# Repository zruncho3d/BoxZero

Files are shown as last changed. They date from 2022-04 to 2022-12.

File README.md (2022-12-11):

# BoxZero - a fully-boxed V0/T0/X0 mod

Simplify, strengthen, and seal your [Voron Zero](https://github.com/VoronDesign/Voron-0) or V0-derived printer ([Tri-Zero](https://github.com/zruncho3d/tri-zero), [Double Dragon](https://github.com/zruncho3d/double-dragon)) by ditching the tophat and moving to a full-box frame.

Mod an existing printer for ~$60 or build a BoxZero from scratch, keeping the 200mm extrusions of a stock V0 frame kit, at about the same cost.

Retains the same footprint as a stock V0, but comes in a bit taller, with more space for the umbilical.

Pairs exquisitely with [Tri-Zero](https://github.com/zruncho3d/tri-zero) (a triple-belted Z mod) and [ZeroPanels](https://github.com/zruncho3d/ZeroPanels) (clip-in, clip-out enclosure panels), both shown in the render and pics below, as well as [Double Dragon](https://github.com/zruncho3d/double-dragon) (the V0 IDEX mod).

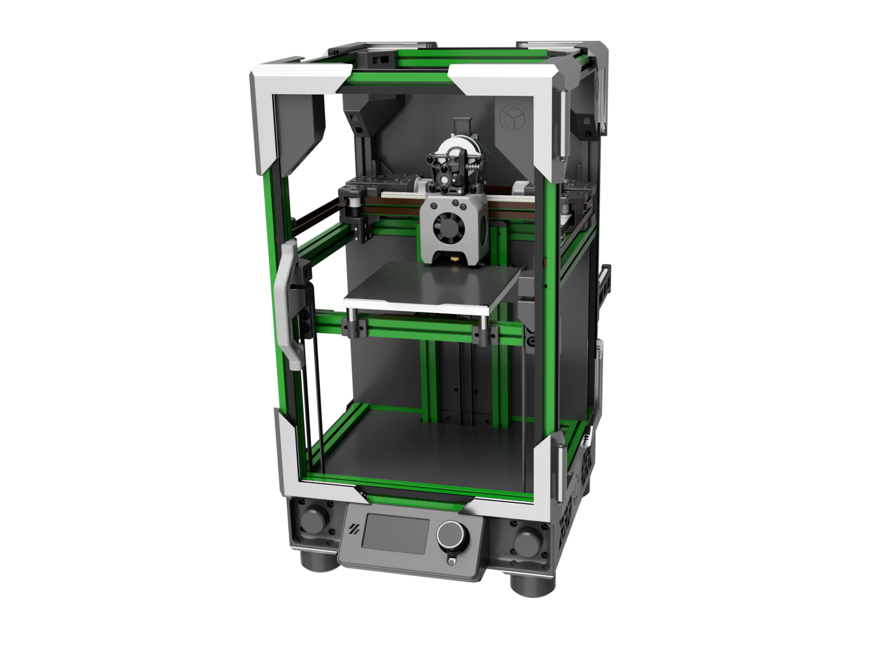
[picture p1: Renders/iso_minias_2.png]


It's real, tested, and reproduced independently the instructions in this repo.  Gallery:

| Zruncho's Green T0 Conversion | Iso View | Red5's Blue T0 Conversion | Iso View |
| - | - | - | - |
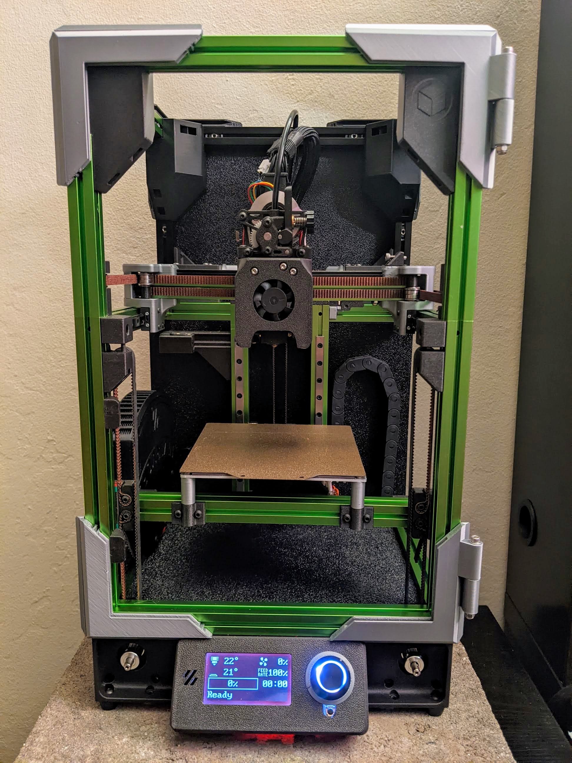
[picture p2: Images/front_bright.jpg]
Front
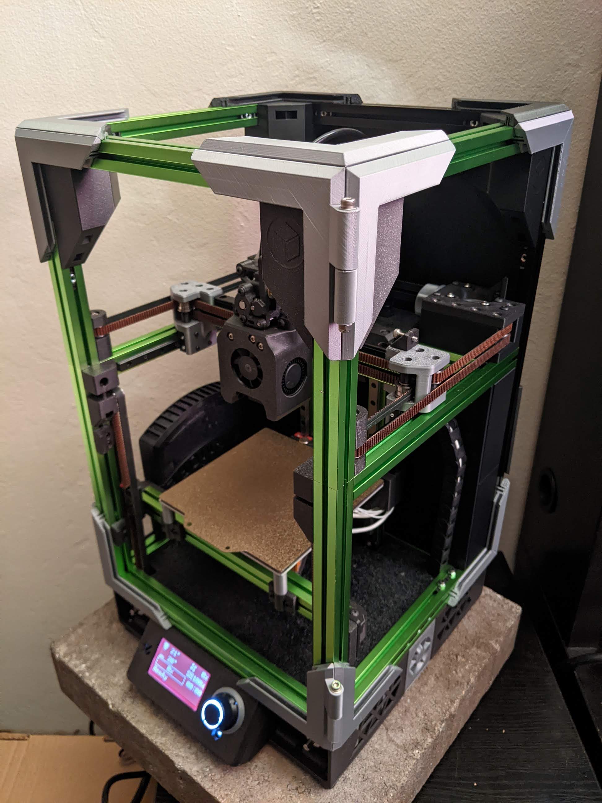
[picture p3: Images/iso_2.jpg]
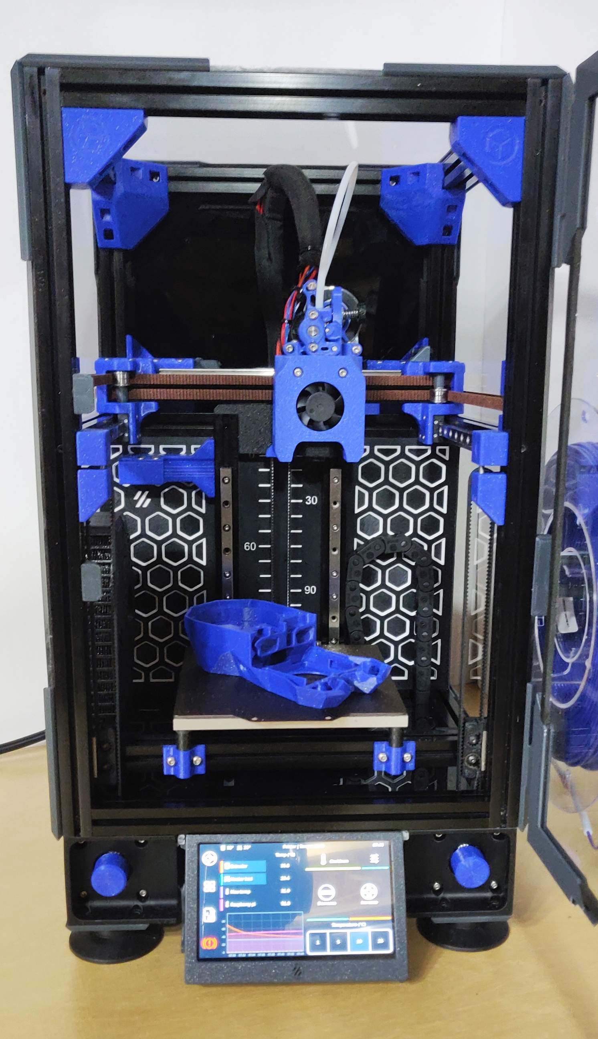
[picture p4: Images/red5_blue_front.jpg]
Front
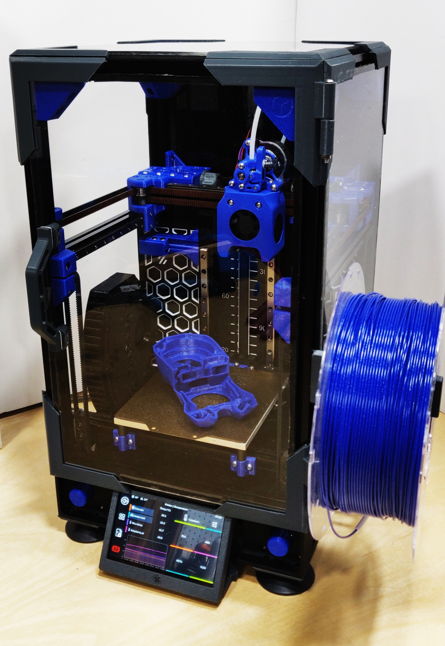
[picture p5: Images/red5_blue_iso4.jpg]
|  |  |  | |

Three key parts make this mod possible:

| AB Blocks (V0-derived) | Front Idlers (Double Dragon-derived) | Top Corners (new, optional) |
| - | - | - |
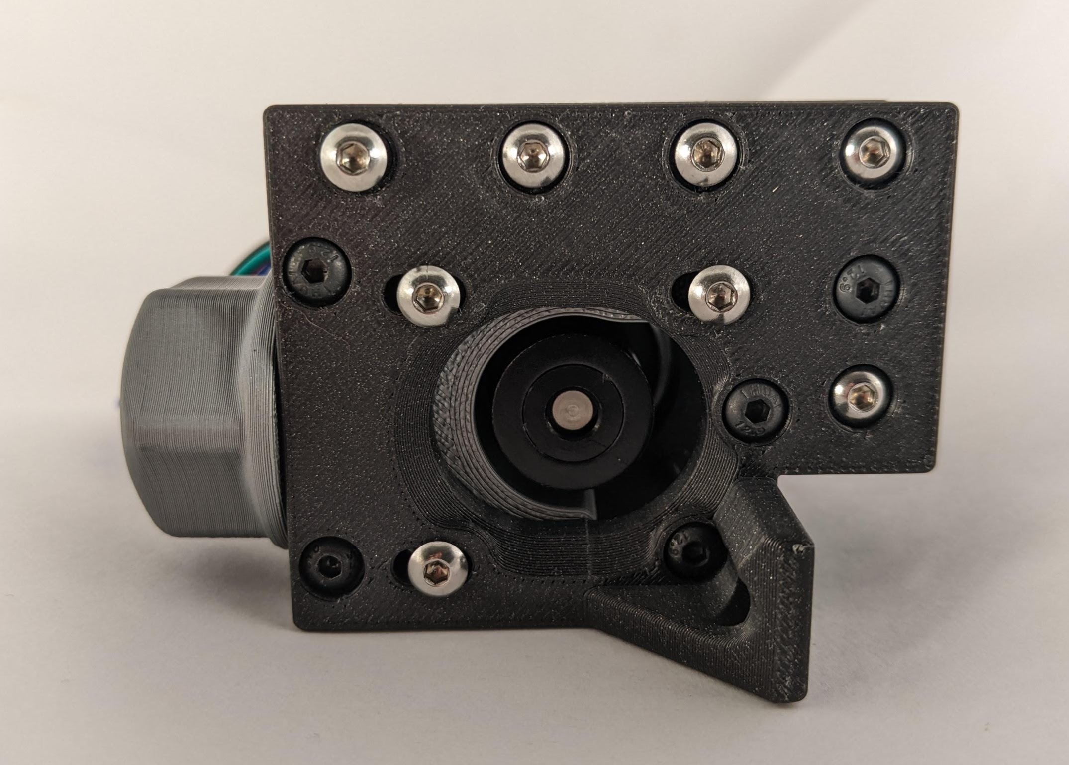
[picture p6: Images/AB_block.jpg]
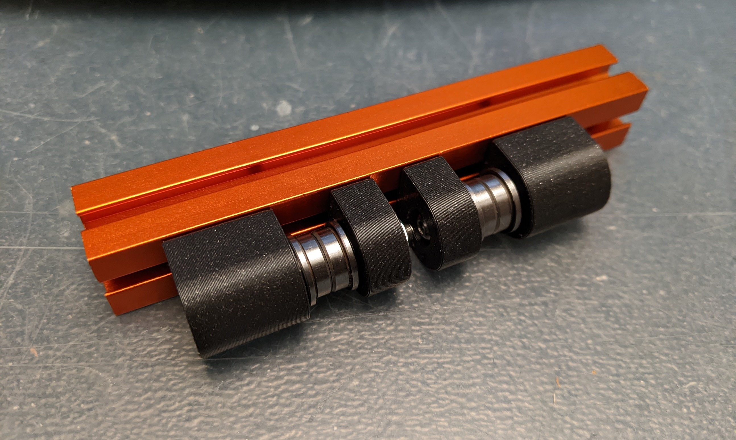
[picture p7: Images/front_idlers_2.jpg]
Front
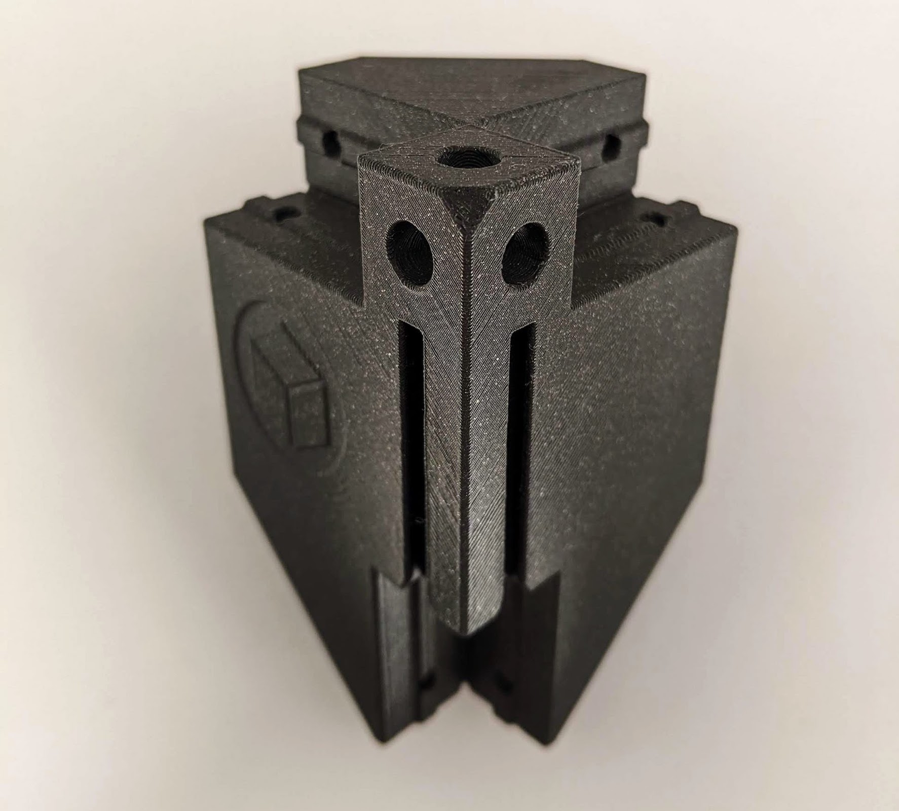
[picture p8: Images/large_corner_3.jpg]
|  |  |  |

Questions?

Join us on the `#tri-zero` channel on the [DoomCube Discord](https://discord.gg/doomcube) - to ask questions, or share your experiences with this mod!

## Updates

#### 2022-04-18 First Release, Alpha-1!

Hello World, BoxZero.

See how it compares, visually:

| BoxZero +TriZero +ZeroPanels +MiniAS +12864 | BoxZero +ZeroPanels | Voron Zero with Tophat (stock V0.1) |
| - | - | - |
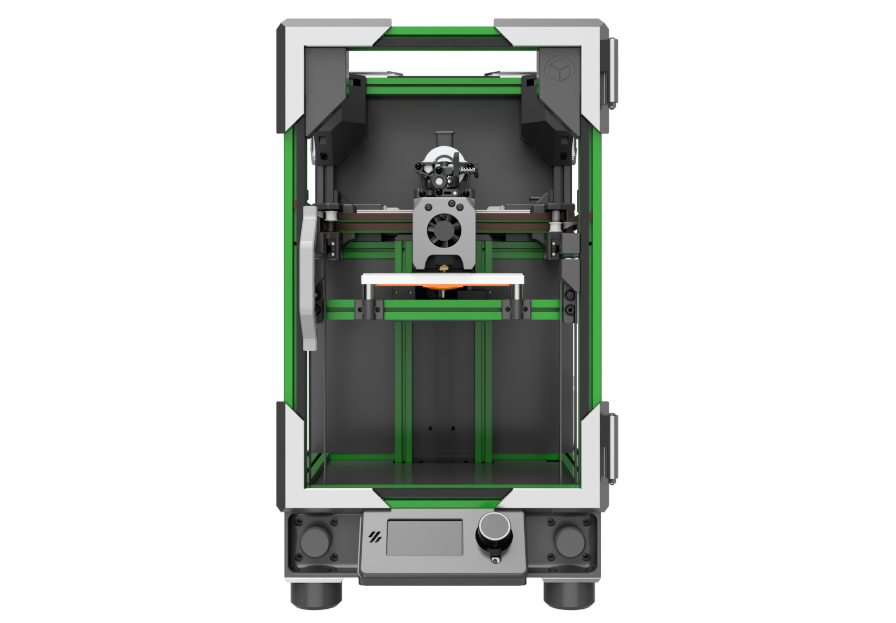
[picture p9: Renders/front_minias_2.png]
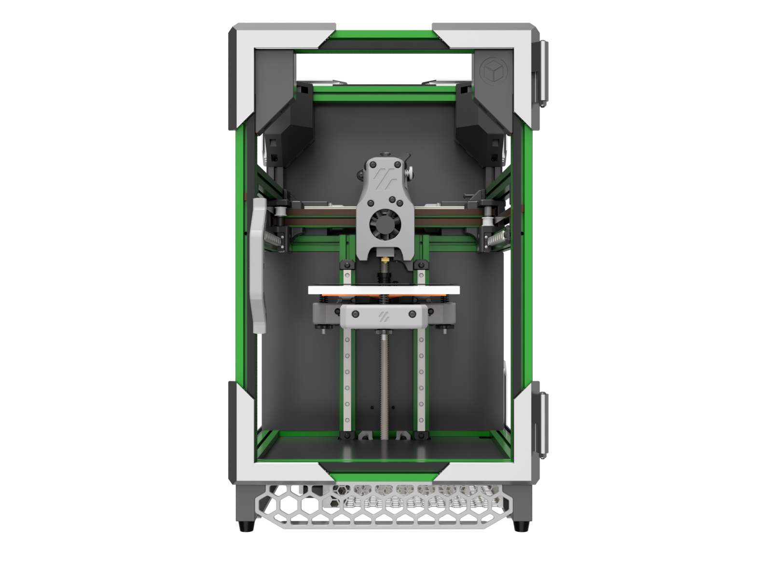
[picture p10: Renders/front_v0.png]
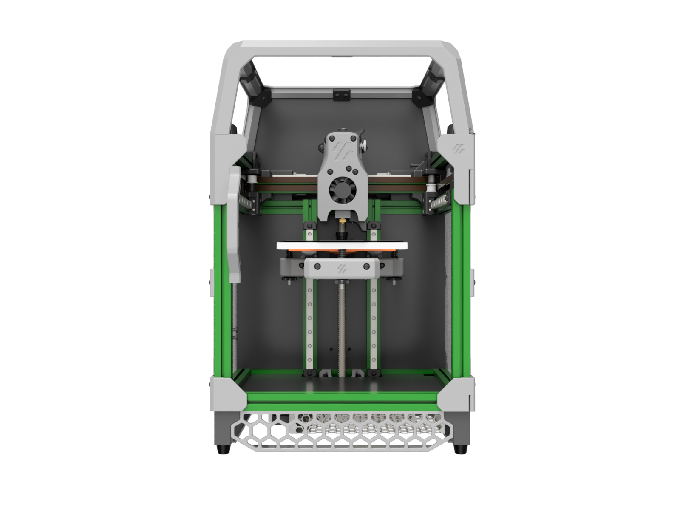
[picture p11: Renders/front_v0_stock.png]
|   |  | 
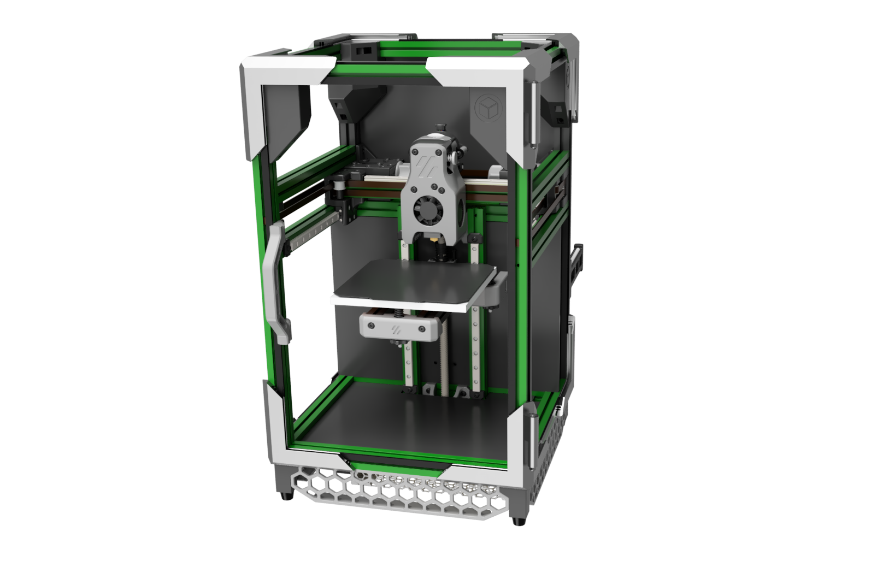
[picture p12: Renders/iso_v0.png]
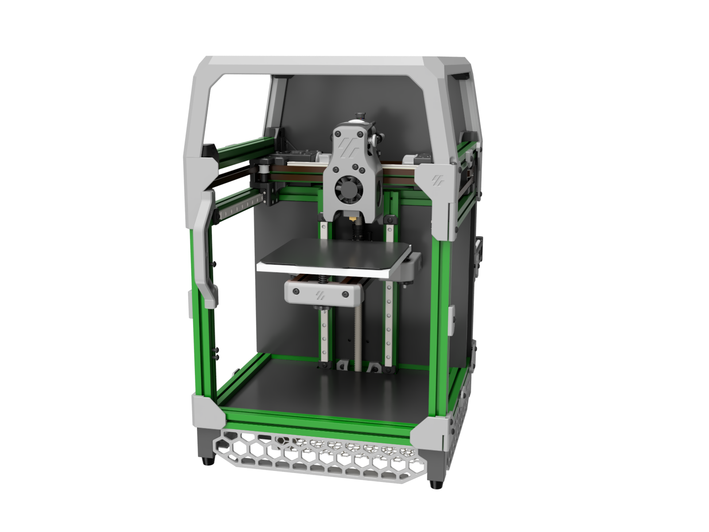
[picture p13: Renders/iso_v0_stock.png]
| Iso  |  | 

## Why this mod?

The V0 tophat serves its function: to enclose the printer.

But ask a bunch of V0 owners... and let's just say, few will express their undying love for the tophat.  

Some actual unsolicited quotes, heard in just the last week:
>  "Yeah, the tophat is kind of the bane of my V0 experience"

> "Can you tell I really dislike the tophat? They started bugging me less after I added a hinged riser that is a solid square. It does not match well enough so it looks bad that way but the stiffness and hinges are what the original should have had."

While I think it looks fine, the V0 tophat creates real quality-of-life issues in practice:
* It's a notoriously challenging print that requires the entire bed of a Voron Zero and good bed adhesion and leveling.
* The small trapezoidal panels are harder to source than rectangular parts.
* The design adds many small parts to print and many heatsets to add.
* To clear the umbilical with some toolhead mods (e.g. [Mini-AfterSherpa](https://github.com/KurioHonoo/Mini-AfterSherpa)), a tophat extension is needed, ideally a [hinged one](https://github.com/zruncho3d/VoronUsers/tree/hinged_tophat/printer_mods/zruncho/Hinged_Tophat_Riser).  But those "censor the view" and require even more parts to print and source.
* It doesn't scale easily.  You can add extensions ([X0 example](https://github.com/zruncho3d/double-dragon/blob/main/STLs/Optional/Tophat_Middle_Spacer_x2.stl)), but you really want to increase the beam thickness too, and not need extensions to fit a V0 plate.
* You can't mount stuff to it easily, at least compared to extrusions (like lights or a camera).

## How does this mod work?

This mod ditches the tophat, moves to a fully-boxed frame, and then updates each part affected by the change to fit best in the remaining space.

### Frame and Corners

You will need additional extrusions to box the frame and make a "fixed tophat".  Don't worry though, you can easily add a hinged top panel, or even just pop out toolless-ly when desired.

Here is the extra extrusion content, visualized:

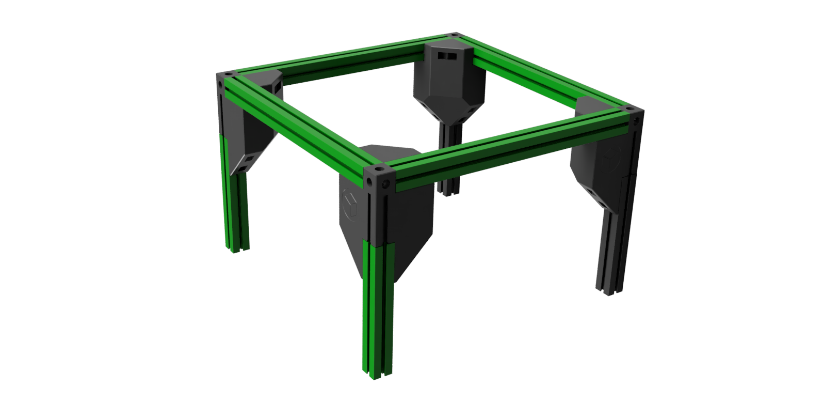
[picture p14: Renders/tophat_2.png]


You can keep your colored extrusions from a V0 frame kit by joining 100mm ones from the bed to 200mm ones in the front.  This repo even includes a printed "extrusion wrench" to join extrusions without marring the surface.

Or, you can use off-the-shelf 300mm-long 1515 extrusions and add the blind joint holes yourself, easily.  With printed corners that add 50mm of height, you'll then have enough clearance for the umbilical.

Or, you can use a full-blind-joints frame with taller extrusions (350mm or taller) and optionally strengthen the corners with corner stiffeners.  These stiffeners are recommended for larger sizes than V0-stock, especially 250mm-length-extrusion printers.

| Large Corner (adds 50mm height) | Small Corner Stiffener |
| - | - |
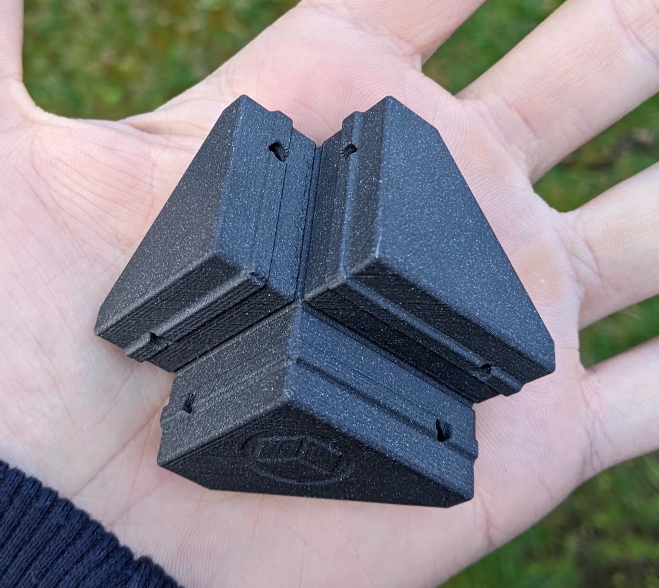
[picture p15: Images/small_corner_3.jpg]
| Front |  |

The V0 side extrusions and bed extrusions get lifted, then other extrusions take their place.  There are a few options:

* **Option A: Replace all verticals with 300s**.  Move 2 of the existing 200s to the top.
* **Option B: Replace the rear 2 verticals with 300s**.  Move 2 of the existing 200s to the top, then add 100mm extrusions to replace the ones for the bed and colorize the front.  
  * If you have a Kirigami bed or T0 mod, the 100s will be easily available.  
  * Conjoin the front 100 and 200mm extrusions with set screws an add 2 200mm extrusions on the side to span the gaps.
  * You'll still need an additional 200mm extrusion for the back.
* **Option C Mix of new 100 and 200mm-length extrusions**.  Effectively, add a fixed tophat like the render above.
* **Option D: Go full-height with cut-to-size extrusions**.  Then use the smaller stiffeners, vs the full-size extrensions.

It all depends on what's easiest to source and what you think looks best.  You choose.  Either way, it should feel super-rigid after.

Note that the corners are asymmetric, with a logo on only one side... we don't want an [M1 situation](https://en.wikipedia.org/wiki/BMW_M1) here.

### AB Blocks

The packaging of the V0 is super-tight, so the big challenge with a full box is fitting the belt path around added frame extrusions.  The key insight was to add extra F623 bearings to redirect the belts around the rear extrusion verticals.  To free up space for the belt, the sliding motor block had to be chopped, but the 3 remaining screws are plenty to fully secure the motor.

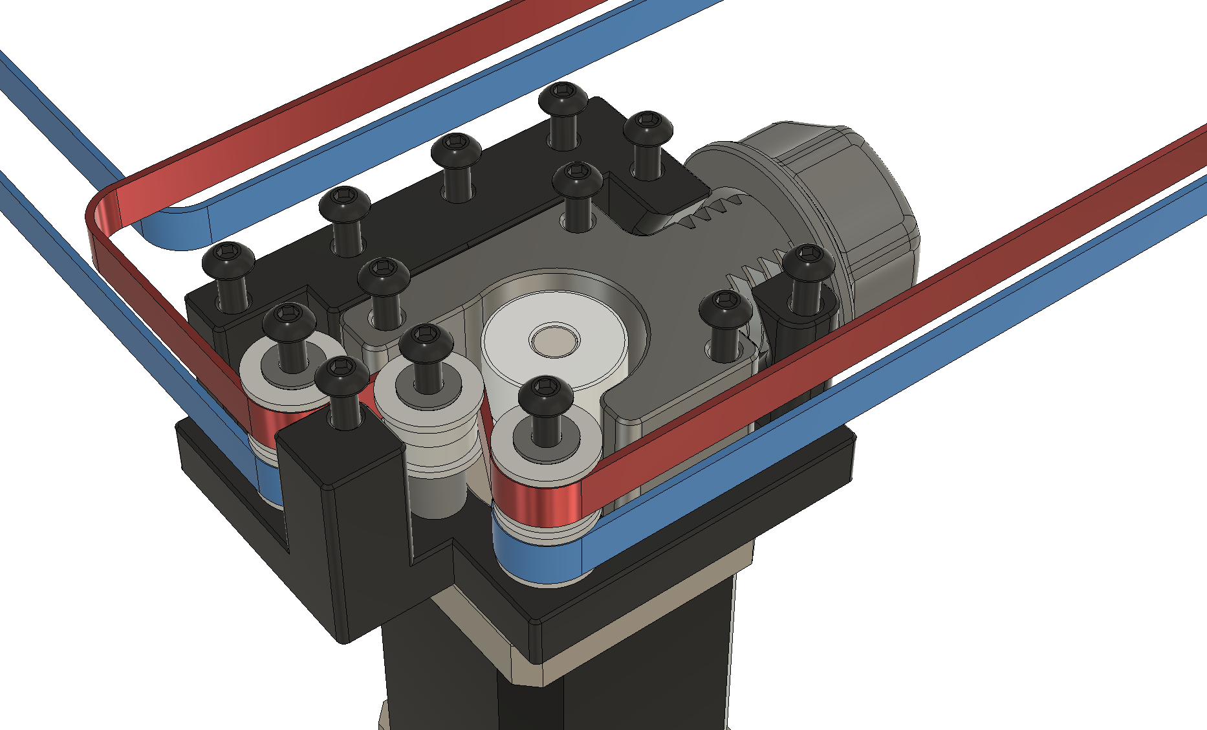
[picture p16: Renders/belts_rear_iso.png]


Top view:

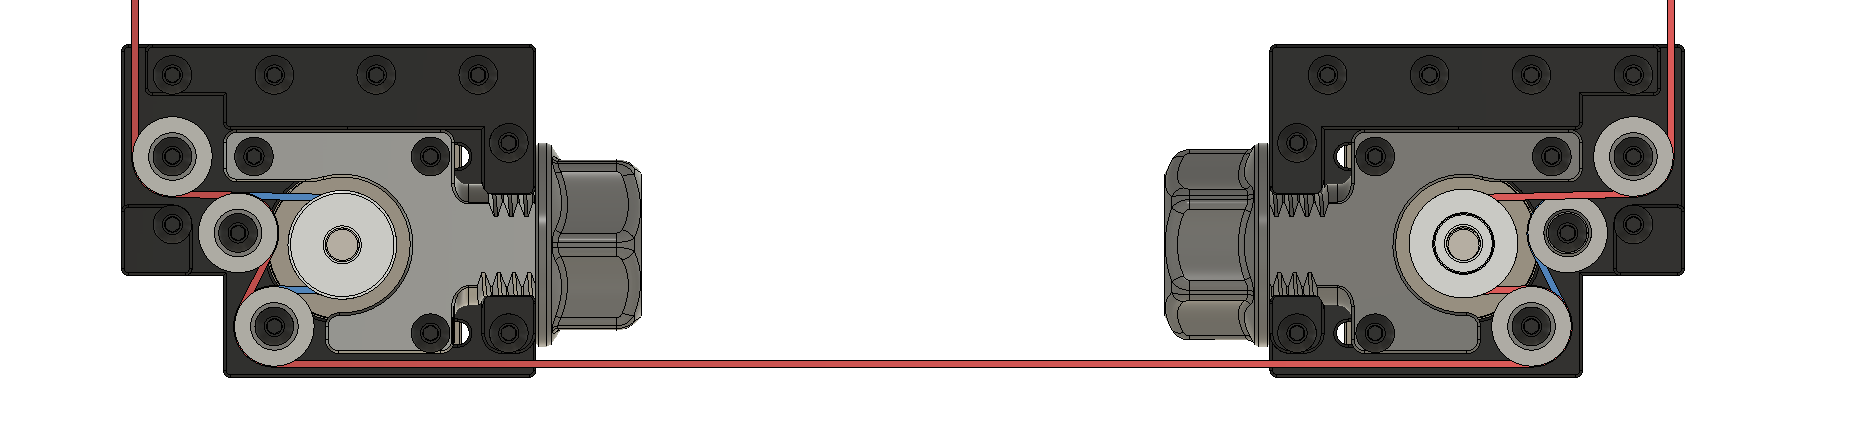
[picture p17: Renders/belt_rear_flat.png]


The complete AB blocks:

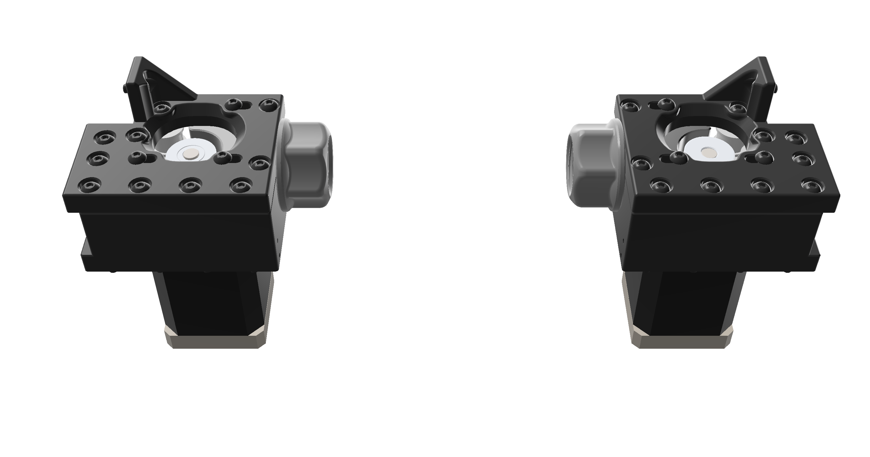
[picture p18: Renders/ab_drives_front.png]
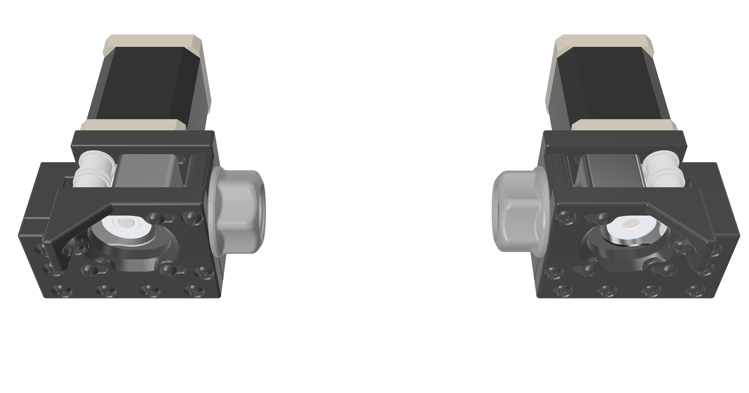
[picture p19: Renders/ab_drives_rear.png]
|  |  |
| - | - |

The new AB blocks are intentionally set back 3mm from the front, to support future mods to add extra Y travel from an offset gantry, so you'll want to add something to bridge that 3mm gap to the Y endstop.  [F0 MGN9 spacers](https://github.com/zruncho3d/f-zero/blob/main/STLs/Gantry/mgn9_spacer_x2.stl) are one easy to span it, especially if using a non-levered microswitch.

The hole positions have been moved too, so that all are aligned easily with 15mm No-Drop nuts.

### Front Idlers

At the front, this mod uses slightly modified [Double Dragon](https://github.com/zruncho3d/double-dragon) front Y idlers for the main belts.

Front

### Enclosure

You can use the default V0 enclosure parts, or much better, can move to [ZeroPanels](https://github.com/zruncho3d/ZeroPanels), which clip in without screws, nuts, magnets, or tape. They're perfect for this application.

[Tecnologic's full boxed-frame enclosure](https://github.com/Tecnologic/ZeroPanels/tree/main/Mods/tecnologic/FlyingZero300), based on the original ZeroPanels, works perfectly here and even includes high-strength, 270-degree hinges.  What's not to love?  You can put the hinges on top too... BAM, and you have a fully accessible toolhead, without even needing 5 seconds to clip out a panel.

| Main Corners | Hinge Corners |
| - | - |
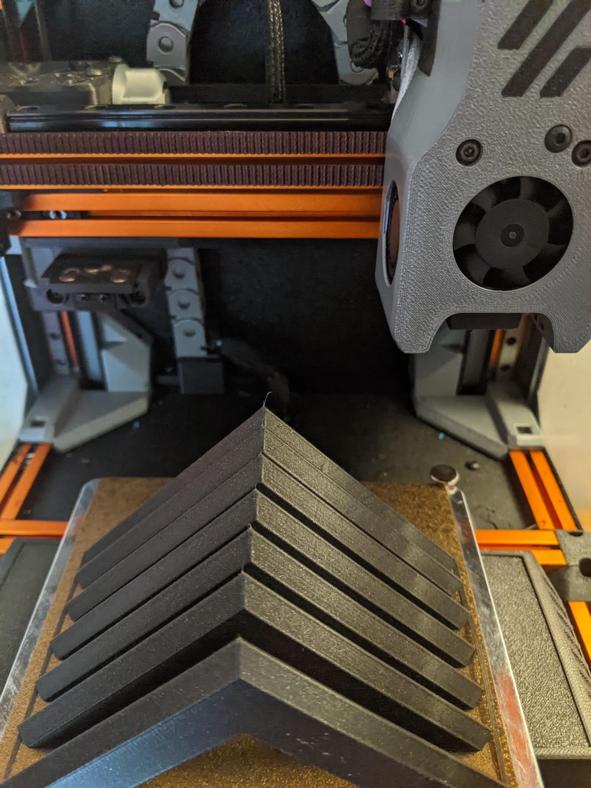
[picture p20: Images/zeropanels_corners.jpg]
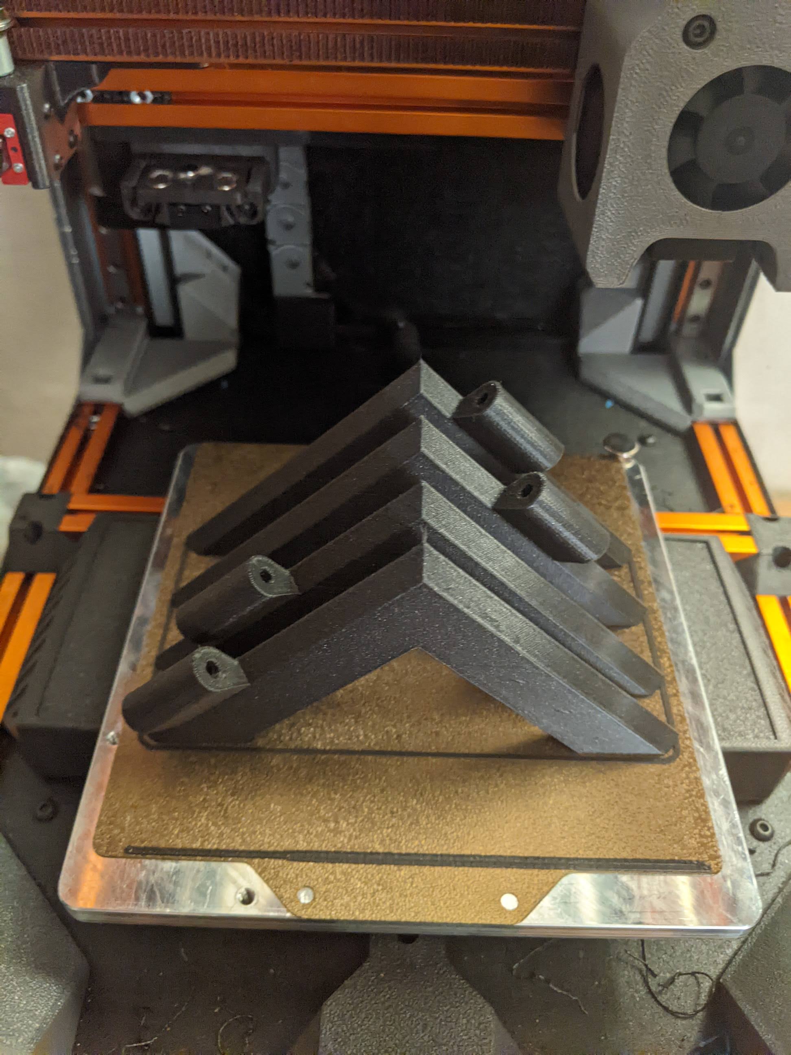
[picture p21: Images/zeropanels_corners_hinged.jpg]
|  |  |

See a video of [ZeroPanels clipping in and out, and then in and out again](https://www.youtube.com/watch?v=L3nBHkO4VzE).

### Other changes

Actually, that's it.  The belt path is shorter, so you can reuse and then trim your existing belts.  The midplate and baseplate don't change.  The rear plate gets lifted up.  It's a good thing, anway, to free up air to cool the Pi mounted back there.

## BOM

These are just the parts beyond those needed for a stock V0.  All assume that no parts comes from the tophat, so they may be really conservative.

| Category | Part | Qty | Notes | Link |
| - | - | - | - | - |
| Fasteners | M3x6 BHCS | 8 to 36 | For corners, depending on style, and how many you add. |
| Fasteners | M3 Nuts | 8 to 36 | For corners, depending on style, and how many you add. |
| Fasteners | M3x30 BHCS  | 2 | For additional bearing stacks in AB blocks |
| Fasteners | M3 Shims | 6 | Combine with the 2 freed by front idler conversions |
| Fasteners | M3 Heatset | 12 | For AB blocks
| Motion | F623 flanged bearing | 8 | For AB blocks
| Panels | 212x332x3mm panel | 3 | Side and front panels, clear acrylic
| Panels | 212x212x3mm panel | 1 | Top panel, clear acrylic

A sample panel order from SendCutSend, without the 15% discount easily found online, looks like this:
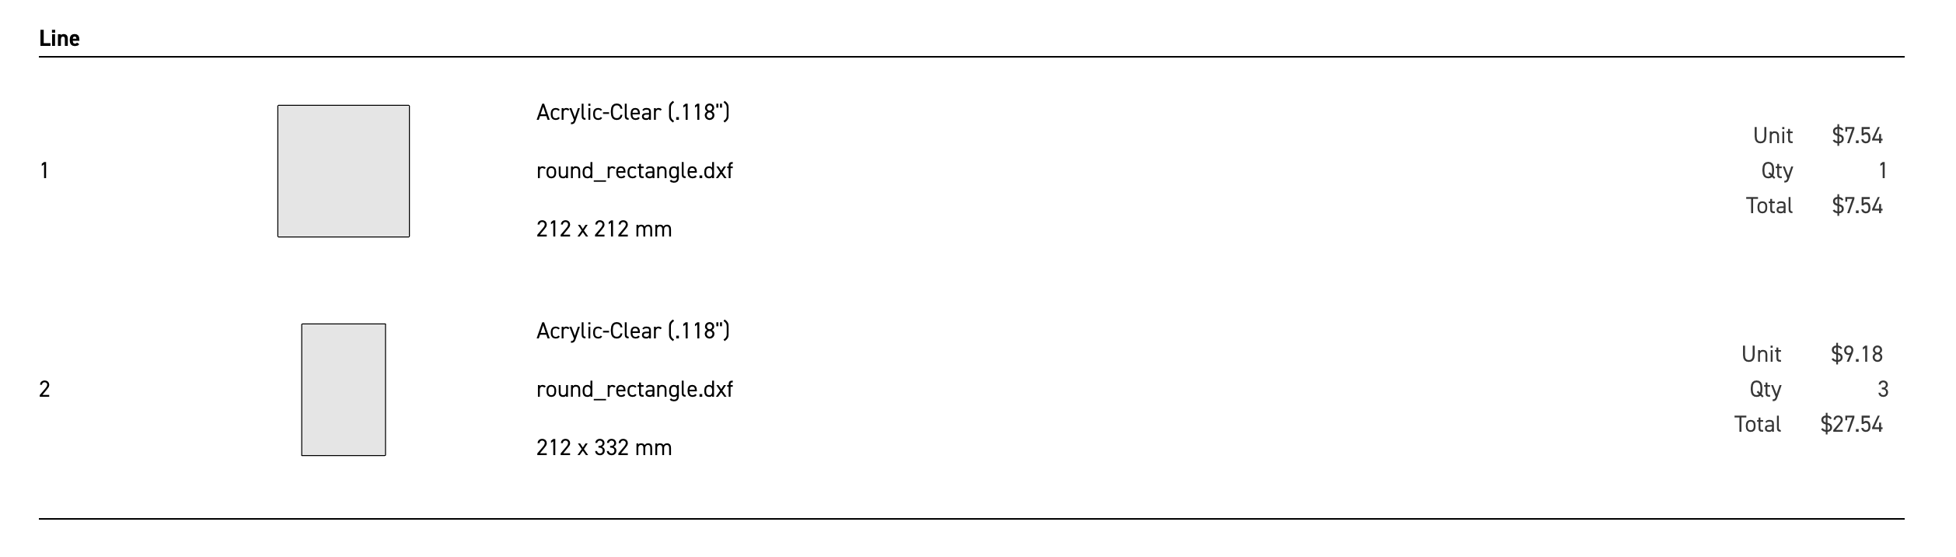
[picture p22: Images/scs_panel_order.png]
iso


For extrusions you have a few choices:

| Category | Part | Qty | Notes | Link |
| - | - | - | - | - |
| Extrusions | 300mm 1515 | 4 | Option A for extrusions | [MBXL 300mm](https://www.amazon.com/MakerBeam-XL-Anodized-300x15x15mm-Pieces/dp/B06XJ5G5QY) |
| Extrusions | 300mm 1515 | 2 | Option B for extrusions | [MBXL 300mm](https://www.amazon.com/MakerBeam-XL-Anodized-300x15x15mm-Pieces/dp/B06XJ5G5QY) |
| Extrusions | 200mm 1515 | 1 | Option B for extrusions | [MBXL 200mm](https://www.amazon.com/dp/B06XHQH9WH) |
| Extrusions | 100mm 1515 | 4 | Option C for extrusions | [MBXL 100mm](https://www.amazon.com/gp/product/B06XJ4T6TW/ref=ppx_yo_dt_b_search_asin_title?ie=UTF8&psc=1) |
| Extrusions | 200mm 1515 | 4 | Option C for extrusions | [MBXL 200mm](https://www.amazon.com/dp/B06XHQH9WH) |
| Extrusions | 350mm 1515 | 4 | Option D for extrusions | Misumi, other |
| Fasteners | M3x20 set screw | 1 per join | Option B/C: join exts; can chop a screw.  20mm length is ideal, 16 is probably fine, and 12 is on edge. |

If making the ZeroPanels exclosure with hinges, you'll also need screws and locknuts for each hinge pair:

| Category | Part | Qty | Notes | Link |
| - | - | - | - | - |
| Fasteners | M3x50 SHCS | 2 per hinge pair |
| Fasteners | M3 locknut | 1 per hinge pair |
| Fasteners | M3 washers | 4 per hinge pair |
| Tape | Foam Tape | | 2mm-3mm adhesive-backed foam tape |

## What's in this repo?

In this repo are all of the STLs needed to do a BoxZero conversion, with just those parts which are not in the V0.1 repo.

All parts should be already be in print-ready orientation, with seam in the +Y dir, and no supports are needed.

Standard Voron settings, or lowered infill and fewer perims, should work fine for most parts:
- 4 perimeters
- 40% infill, depending on the part
- 0.2mm layer height

The AB blocks can be printed with much less infill (20%).

Print the corners (both types) with 3 perims, 10% infill or higher.  While this will print happily with zero infill, you don't want flexible edges.

### Printed Parts

Print all STLs in the quantites noted from this repo, along with STLs from:
- [ZeroPanels](https://github.com/zruncho3d/ZeroPanels)
  - Regular V0 ZeroPanels parts work fine.
  - [Tecnologic's full boxed-frame enclosure](https://github.com/Tecnologic/ZeroPanels/tree/main/Mods/tecnologic/FlyingZero300) are recommended for easier front sealing.
  - When printing the hinges, use 4+ perimeters for strength, plus some infill (13% or more).
  - **NOTE:** These parts should be sized to exactly match your panels and your foam tape.  Use the F360 file if you can; you don't want the ZeroPanels to slide out, or not attach properly, because the foam tape is pushing back too much.  In Zruncho's case, the default foam tape gap of 1.8mm was way too small for 3.1mm (1/8") foam, and the panels bow out or don't close as desired.  Easy-enough fix - the ZeroPanels CAD is parameterized and documented - but watch out.
- [F-Zero](https://github.com/zruncho3d/f-zero): [No-drop nuts](https://github.com/zruncho3d/f-zero/tree/main/STLs/NoDropNuts) are highly recommended, specifically the no-grip flat-top ones

## Assembly Notes

### Frame

- Joining extrusions (typically for 100 mm + 200 mm -> 300 mm):
    - Print the 1515 extrusion wrench and use it.  It will protect the sensitive anodized finish of the extrusions, vs using an adjustable wrench or vise, both of which will damage the surface finish.
    - Use a 12mm m3 set screw or make one by chopping the end off of a screw with a hack saw or Dremel. Tighten the set screw into the extrusion threads by 6mm or so, and then using an allen wrench, block it from screwing down further.  
    - Then, screw on the small extrusion.  Once you feel resistance, go slow, and use the extrusion wrenches to align to the next quarter-turn.  No loctite should be needed for the set screw, as the aluminum should slightly deform as you add pressure to get the final quarter-turn.  Don't go too hard and destroy the threads, but don't fear: the aluminum will yield before the steel does.

- To add a hole for a gantry horizontal extrusion into a 300mm vertical, put the 100mm extrusion against your V0 frame-drilling guide, where the guide has been screwed onto the end.  Then, use the hole in the extrusion wrench (see the `STLs/Tools` directory) for alignment to 7.5mm from the end of the 100mm vertical.  Don't forget to drill holes in the other ends of the frame joints, too, if these are fresh extrusions.  

- For the full-height verticals option, put holes in the ends, 7.5mm from the edge.  These are not needed with 300mm extrusions and the frame corners.

- Make sure to add all the NoDropNuts you'll need before, before closing up corners.
  - Add to rear verticals for rear attachments like spool holders or filament guides.
  - Add two on the inner faces of the rear verticals, which will attach to the upper AB blocks.
  - Add one for each hole in the corner stiffeners you intend to use.

- Both corner block types are *designed* to be tight, and in fact, matched to fit your exact extrusions!
    - You will have to scrape away some of the plastic that goes into the extrusion slot to get them to fit.  This is fully intentional, so that extrusions that are nearly 3.0mm in slot width, up to much sloppier ones (3.6mm or so), can be accommodated, and so that screws become optional, and not even required.  The edge of an extrusion should be sharp enough to peel away a bit of the edge.  Go slow and apply pressure, then back off and clear out the peels.  

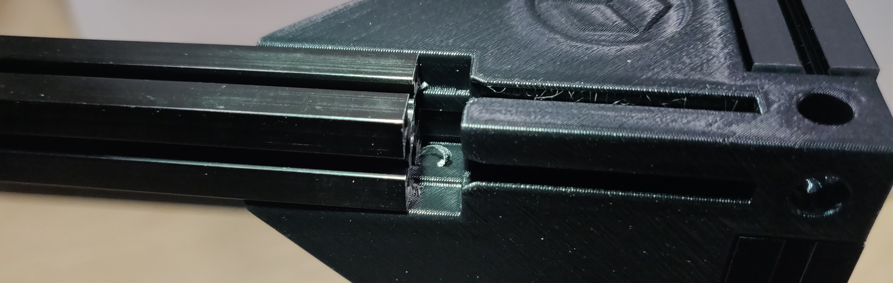
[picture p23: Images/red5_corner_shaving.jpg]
    

    Note the curl above?  The flat edge of the inside of the slot, as well the sharp corners, will look like this (good!):

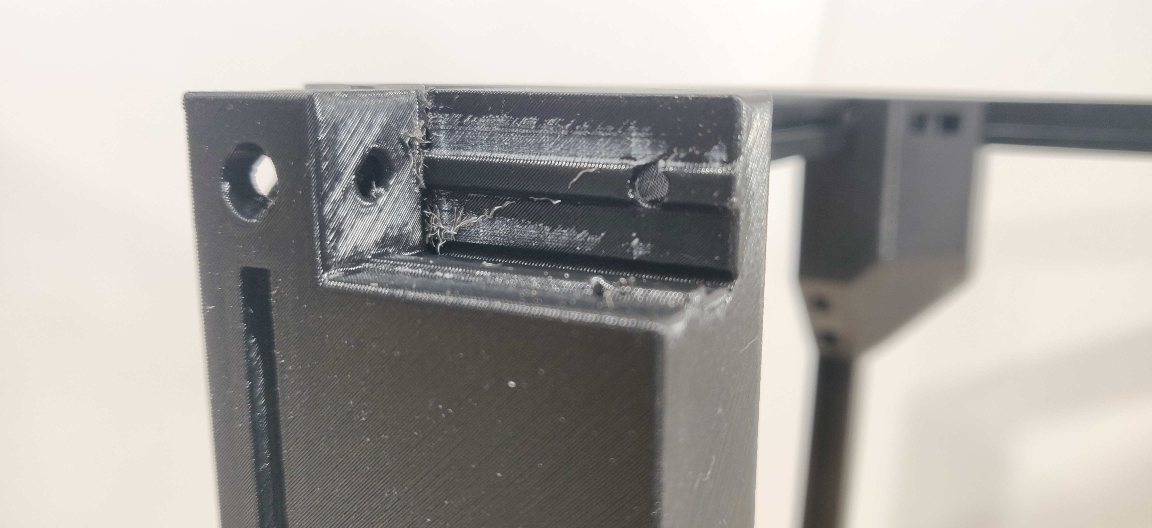
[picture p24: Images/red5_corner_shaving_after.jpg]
   

   To get the extrusion started into the corner, twist the extrusion into the inner corner to get started, and then keep it parallel.  If one side "escapes", start over and work inwards.

   **The extrusion should fit tightly, without screws.**

    Look ma - no screws!

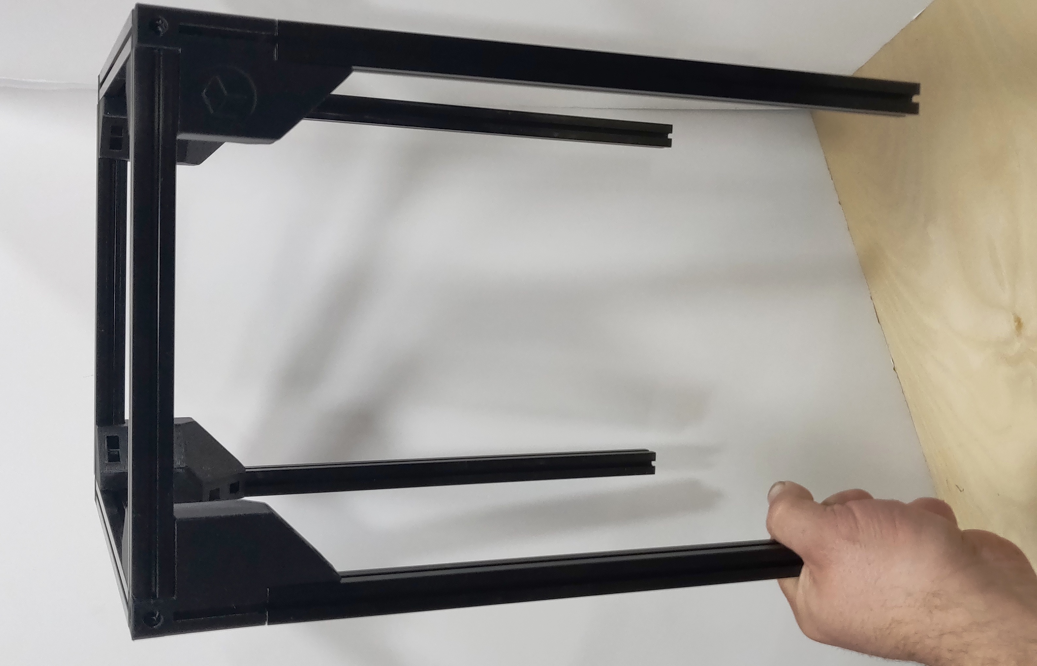
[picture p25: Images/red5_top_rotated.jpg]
    

    - Most corner screws are optional.  The top-most 12 on the frame are the most important (4 down from the top, and 2 in each corner, sideways).  Beyond this, one or two per corner below should be plenty to add rigidity, but you can add an extra 4 per corner if you want.  If so, make sure to pre-load no-grip NoDropNuts first, in a visible location, so that you can slide them in.

- Build the top crown of extrusions and corner blocks, then slide it on top.
- Add the screws later whe you're sure all the nuts are in the right place.

### AB Blocks
* Build the modified AB blocks similarly to V0 AB blocks, using with the pics above or V0.1 manual for reference.
  * Press all heatsets flush and make sure to add washers around each F623 bearing stack, but not the 9mm spacers.
  * Protip from Red5: use M3 nuts to secure the bearing and washer stacks with the AB upper parts, temporarily, and then remove the temp nuts right before building the full assembly.
* Access to the belts is easiest when the AB blocks are outside the frame.  Toothpicks work well to get the belt where you want it.  Route the belts, then add the blocks to the frame.  You don't have to do it this way, but if you build the blocks first, the frame verticals won't get in the way.

### Front Idlers
* Note that one of the needed washers is built into each part.  Make sure to tighten the screw only when the idler unit is being pulled against the extrusion.  It will be under tension from the belt, and you don't want it shifting when that tension is added.

### Converting

If converting, note that you don't need to take the frame apart!  Verticals can slide up and out.  You can leave all the electronics, gantry, etc. in place.

### Caveats

If using a Mini 12864 display, with a mount like [the one used with Tri-Zero](https://github.com/zruncho3d/tri-zero/blob/main/STLs/Optional/12864_Mount_x1.stl), the knob sticks out a bit, and it may interfere with a Tecnologic-style ZeroPanels enclosure hinged front.  A workaround is to x-acto around the lower edge of the panels, to create a bit of a gap, or fix it in CAD.

## FAQ

### What do you mean by Alpha Release?

The parts actually work, and have been tested in a working printer.  But sizes and parts may change in future releases.

### What are the downsides?

- Potentially a less rigid frame when using ZeroPanels, since the panels float in the extrusion slots, vs more rigidly mounted enclosure panels.  This is somewhat counteracted by closing the box and adding stiffening corners though.  Perhaps some thumbscrews for the panel clips could be a nice middle ground.

- The belt path is a bit more twisty and tight around the motor pulleys, so it's more sensitive to alignment errors.  You'll know quickly if your pulley is not quite aligned, as it will make a sound when in motion on the side that's running.  You can have a pulley that's good enough for a regular V0, but then when converting to BoxZero, the shorter paths may reveal the alignment issue.

- A little more cost, at least compared to a V0.  Just a little.

### What is the cost?

It's almost a cost-neutral mod for new builds.  The outer enclosure panels get slightly larger, but then you don't need laser-cut trapezoid panels.  Add the cost of a few bearings and some extrusion.

### What if I have questions?

The renders and CAD should answer many questions first.

Then, go the DoomCube Discord and ask on the `#tri-zero` channel.

### Convince me!

Still not convinced?  For a V0/T0/X0 build, here are the benefits:

**Simplicity**
* Rectangular panels are easy to source from anywhere.
* A full box is straightforward to seal.

**Maintainability**  
* You can build the frame first, then add the AB blocks (the ones with motor tensioners) later, or swap them for future mods.

**Rigidity**
* A metal front-top crossmember adds rigidity, vs nothing (V0), or a plastic tophat.  
* A metal box top adds rigidity in general.
* The added rigidity enables greater scalability, too, especially to +50 X/Y/Z, which can enable the use of commodity Prusa-Mini-size 180mm beds.  This is the super-secret ulterior motive of this mod...

## Related Work

- [Hartk1213 Hinged Hat for the V0](https://github.com/VoronDesign/VoronUsers/tree/master/printer_mods/hartk1213/Voron0_Hinged_Top_Hat) - solves a real problem, but requires many printed and non-printed parts.
- [Zruncho Hinged Tophat](https://github.com/zruncho3d/VoronUsers/tree/hinged_tophat/printer_mods/zruncho/Hinged_Tophat_Riser) - a great implementation of the wrong solution :-)
- ... and many, many other tophat mods on VoronUsers.  It's almost a V0 rite of passage...
- [DooMini](https://github.com/TigranDesigner/Voron-Mods/tree/main/DooMini) - similar goal, different method, more filament used.
- [F0 Corner Blocks](https://github.com/zruncho3d/f-zero) certainly inspired the corner blocks here.  BoxZero ones are better.

## Credits

- Thanks to Red5 on Discord for being the first to print, providing useful feedback for the first release, and sharing pics included above.
- Thanks to Clee for reviewing the README and test-printing parts in advance.

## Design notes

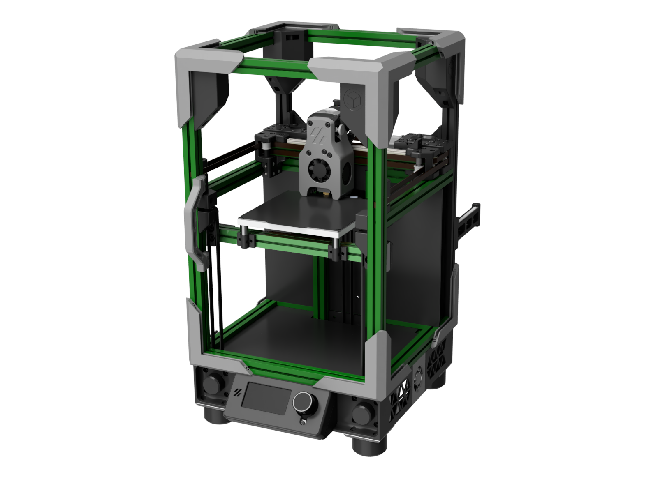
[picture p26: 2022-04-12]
Renders/iso_green_t0.png

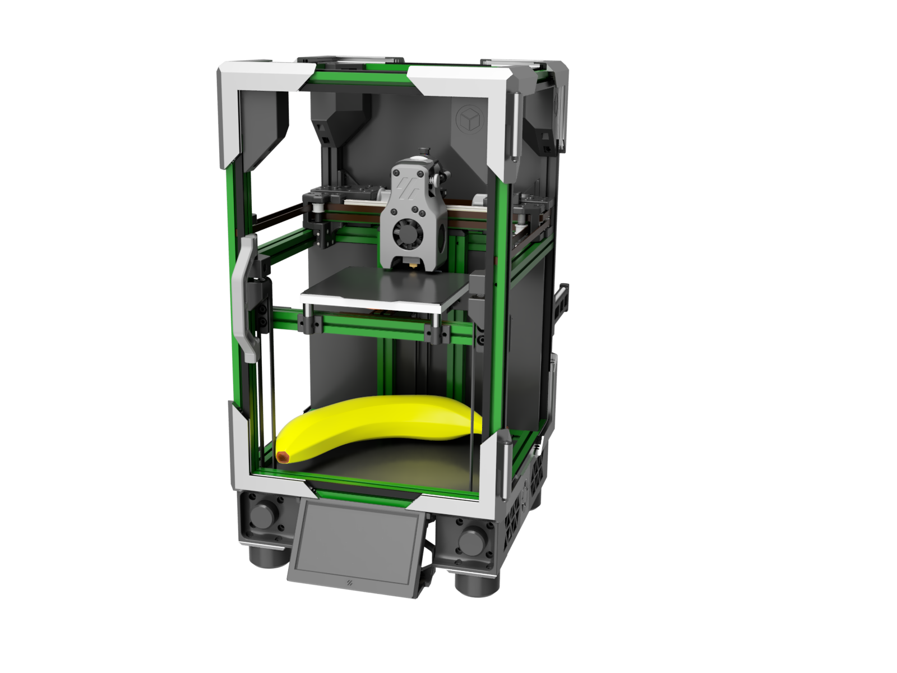
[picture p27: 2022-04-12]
Renders/banana_for_scale.png

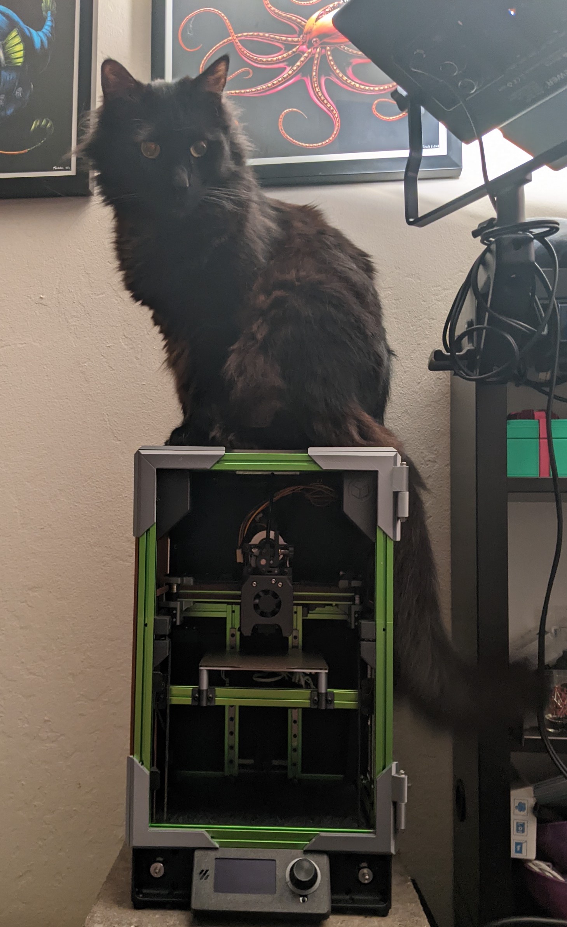
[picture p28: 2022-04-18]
Images/the_foos_approves.jpg

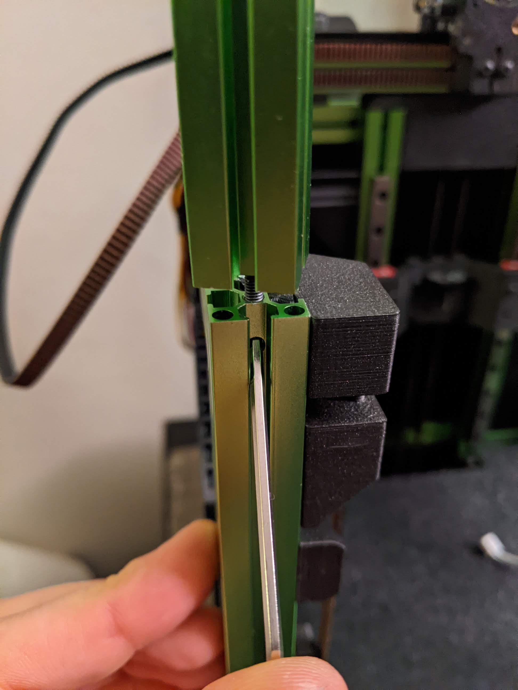
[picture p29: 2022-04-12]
Images/joining_extrusions.jpg

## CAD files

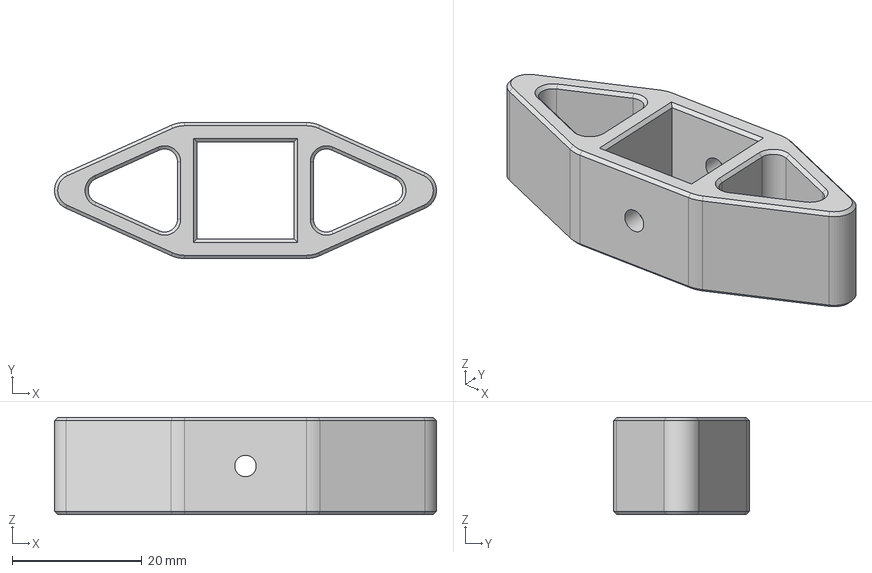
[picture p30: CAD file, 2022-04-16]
CAD/Extrusion_Wrench_1515.step
59.0 x 21.0 x 15.0 mm

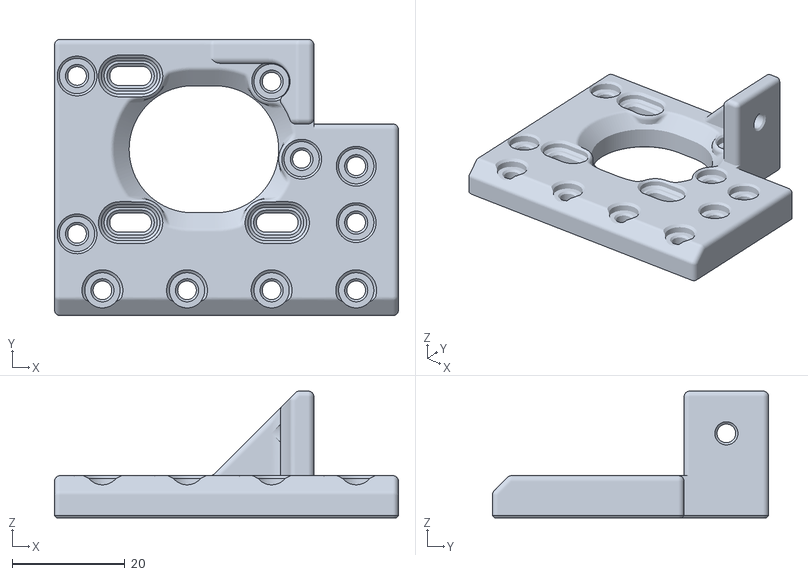
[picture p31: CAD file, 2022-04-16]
STLs/B_Drive_Frame_Upper_x1.stl
61.0 x 49.0 x 22.5

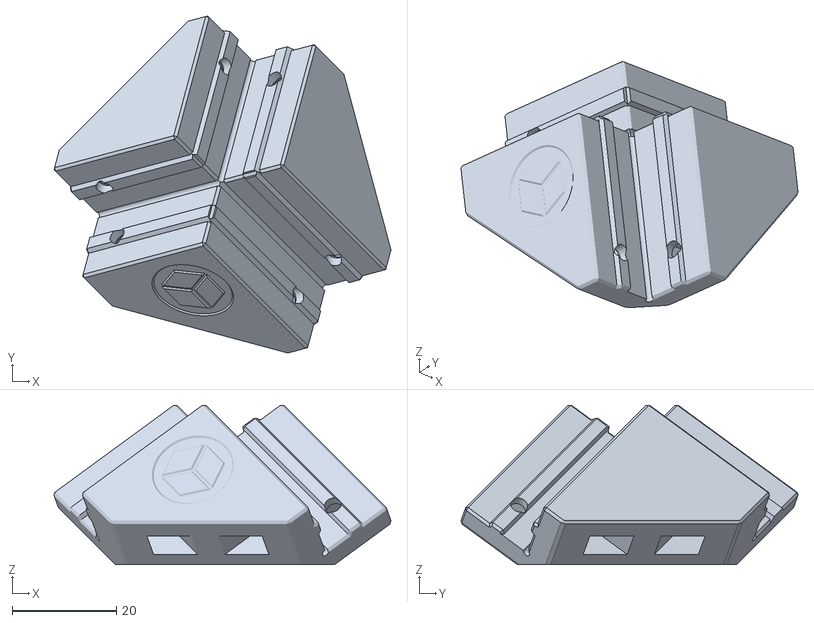
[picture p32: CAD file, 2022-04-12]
STLs/Top_Corner_Mini_x4.stl
64.7 x 64.7 x 30.6

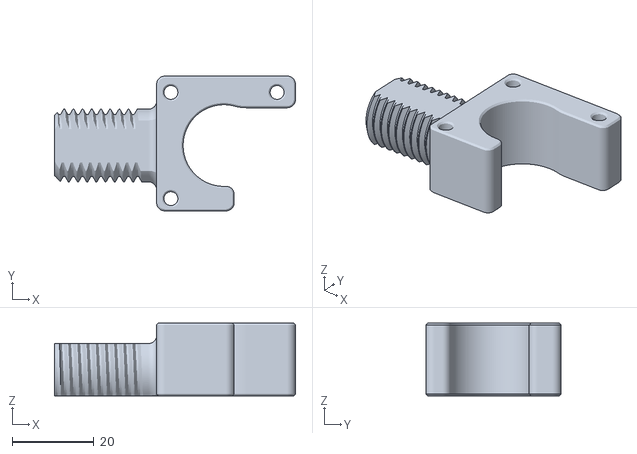
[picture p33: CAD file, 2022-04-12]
STLs/[a]_A_Drive_Tensioner_x1.stl
59.0 x 33.0 x 17.8

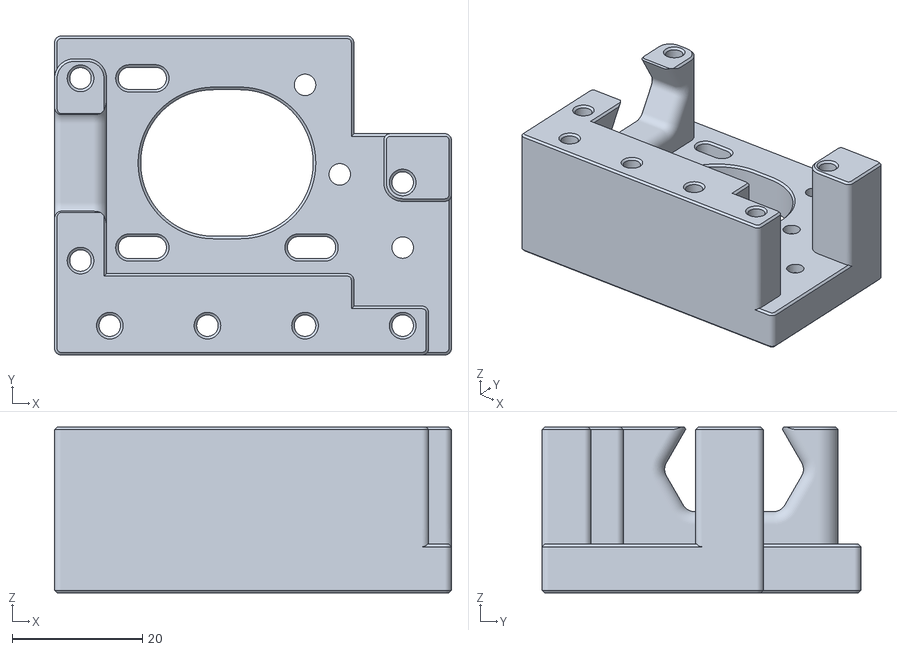
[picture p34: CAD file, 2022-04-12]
STLs/A_Drive_Frame_x1.stl
61.0 x 49.0 x 25.5

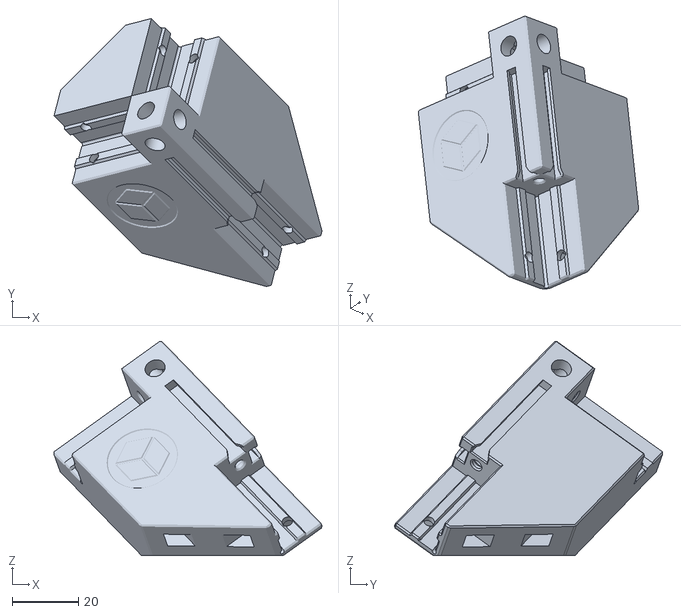
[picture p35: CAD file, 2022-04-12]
STLs/Top_Corner_x4.stl
81.2 x 81.2 x 64.9

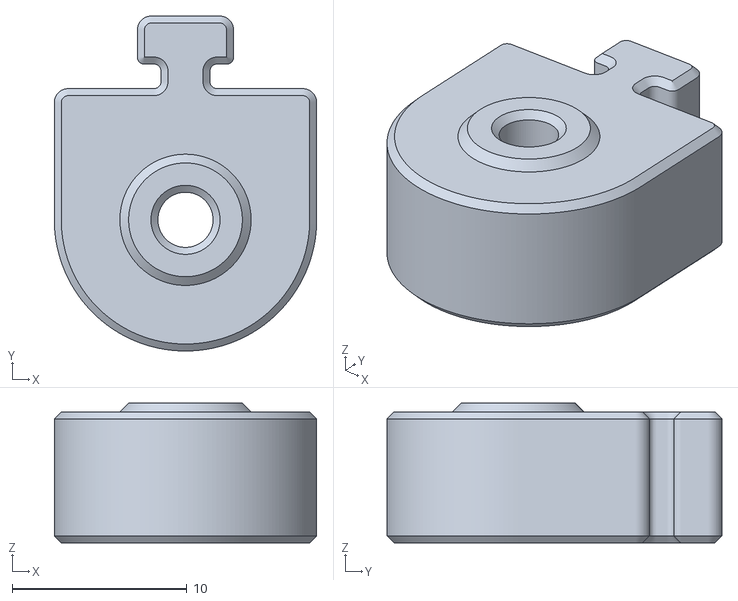
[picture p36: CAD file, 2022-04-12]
STLs/Front_Idler_Right_Lower_x1.stl
15.0 x 19.1 x 8.00

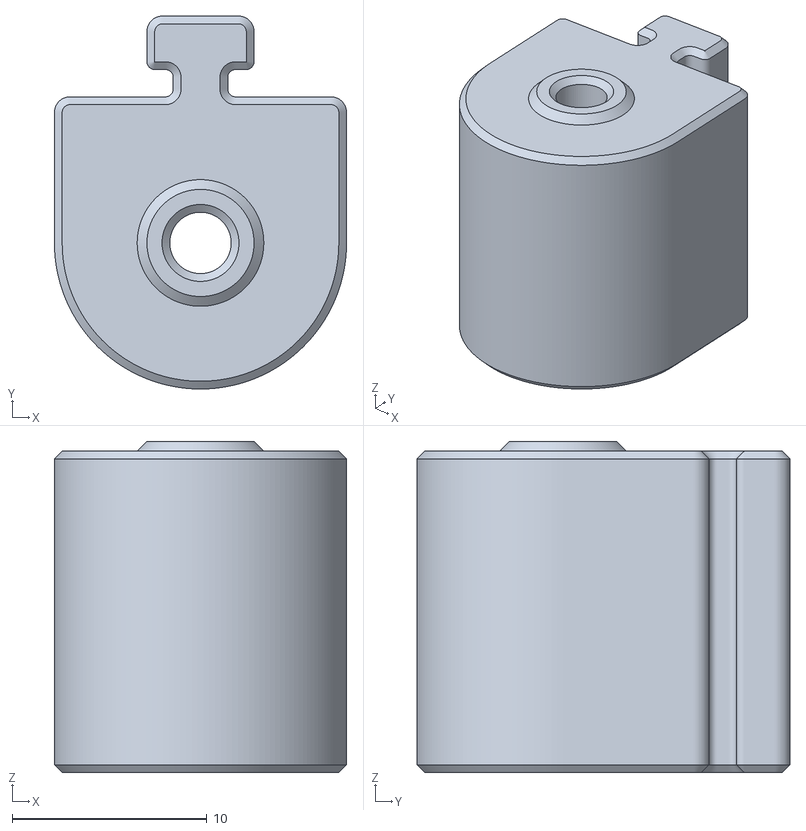
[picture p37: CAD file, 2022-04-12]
STLs/Front_Idler_Left_Lower_x1.stl
15.0 x 19.1 x 17.0

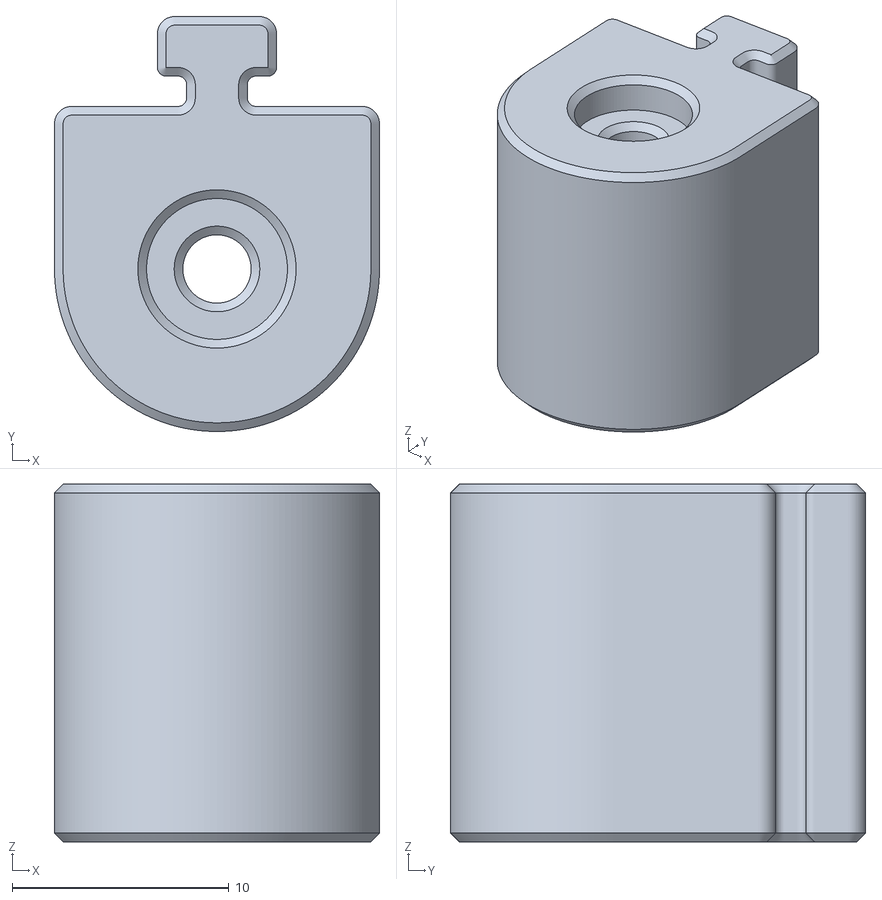
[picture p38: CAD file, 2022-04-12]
STLs/Front_Idler_Right_Upper_x1.stl
15.0 x 19.1 x 16.5

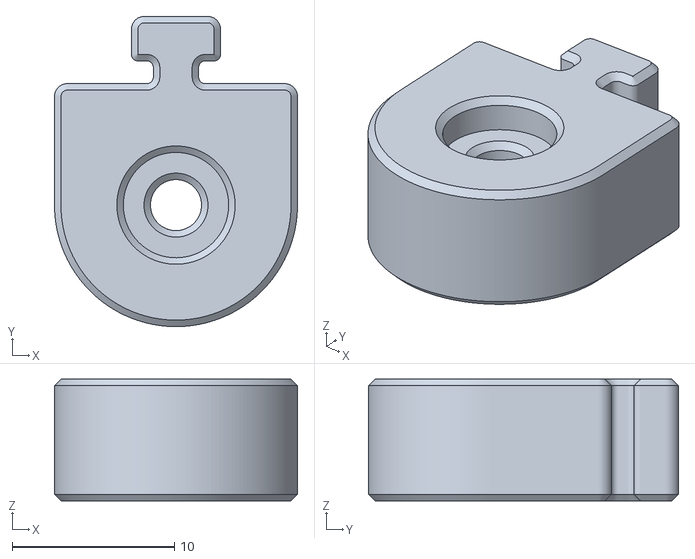
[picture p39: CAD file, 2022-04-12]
STLs/Front_Idler_Left_Upper_x1.stl
15.0 x 19.1 x 7.50

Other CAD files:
STLs/Tools/Extrusion_Wrench_1515.stl
STLs/A_Drive_Frame_Upper_x1.stl
STLs/B_Drive_Frame_x1.stl
STLs/[a]_B_Drive_Tensioner_x1.stl
CAD/Extrusion_Wrench_1515.f3d

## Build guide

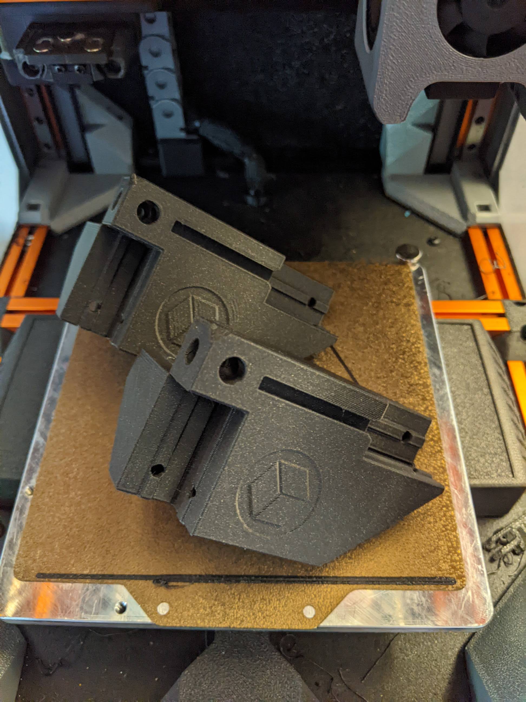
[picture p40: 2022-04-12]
Images/printed_corners.jpg

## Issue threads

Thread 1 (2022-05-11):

Top_Corner_x4 Bridging Issue

PedroC1999, 2022-05-11:
Whilst slicing, it is shown that the bridges for the slot holes are not on a flat plane, which causes issues when bridging and printing.
Nothing that can't be fixed with a quick snip or even a minor pull of the plastic, but do expect a tiny amount of clean-up.

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

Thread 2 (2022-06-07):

Small mid-air extrusion near tops of Top_Corner_x4.stl

kyleisah, 2022-06-07:
Prusaslicer ver. 2.4.2, 0.2mm layer height, Layer 283 (Z 56.6) there's a little floaty bit where the screw holes begin bridging together.

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

I *think* if you either size-up or size-down those holes, you could get that very small problem to slice correctly. Definitely not a problem if a little blob sticks to a wall, but I figured I'd let you know. :)

kyleisah, 2022-06-07:
I sliced this with my usual settings, 4 walls, etc. But the issue persists when using the recommended print settings in the README

kyleisah, 2022-06-07:
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
 Hurts the eyeballs less 😄

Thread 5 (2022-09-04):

Doc Issue: screws needed

zruncho3d, 2022-09-04:
Reported by DrawnToLife on Discord:

sorry - now that I've done most of the conversion (A/B blocks built, extrusions swapped out, just putting the gantry back together now but idlers and what not are in place), let me clarify

the original A/B blocks use all M3x35, so you actually need 6 new new M3x30 screws to build the new A/B blocks, not just 2 (b/c you can't salvage any screws from any of the other conversion steps)

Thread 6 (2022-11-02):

The names of the A and B Drive Frame Upper stl's seem to be switched.

Sir-Storm, 2022-11-02:
It's honestly not a big issue as you still end up with all the right printed parts, it just caused me a bit of confusion when I went to slice them. It could maybe cause someone to print the wrong part if they have to reprint one of them.

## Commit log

2022-04-12 First Commit for BoxZero
    [A_Drive_Frame_Upper_x1.stl, A_Drive_Frame_x1.stl, B_Drive_Frame_Upper_x1.stl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]
2022-04-16 Tweak AB upper to improve motor-screw engagement and add clearance for MGN9 gantries
    [A_Drive_Frame_Upper_x1.stl, B_Drive_Frame_Upper_x1.stl]
2022-04-16 Update extrusion-joining wrench with hole guide
    [Extrusion_Wrench.stl, Extrusion_Wrench_1515.f3d, Extrusion_Wrench_1515.step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]
2022-04-18 Add pics + belt renders; update README
2022-04-18 Add CAD
2022-12-11 Update set screw length recommendation
    Thanks to mjonuschat from #tri-zero - matches my experience that longer is better here to get a solid connection.
